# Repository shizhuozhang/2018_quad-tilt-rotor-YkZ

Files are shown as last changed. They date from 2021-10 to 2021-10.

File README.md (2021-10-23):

# <center>小型四倾转旋翼模型机

# (a small scale quad-tilt-rotor prototype)<center>  

&emsp;&emsp; 该项目资助来源于哈工程 (HEU) 自动化学院 2017年的大学生创新创业训练计划的项目，项目经费1万元左右，后该项目延续为我的本科毕业设计。启发来源于美国”鱼鹰V-22“倾转旋翼机和中国在研的“蓝鲸”四倾转旋翼机。由于经费有限，时间有限，资料有限，当时的个人能力有限，仅完成模型机的初步实现，包括：机械模型的设计制作（感谢EV刘同学的帮助），整体电控系统的设计，一个简单的地面站上位机（感谢EV燕同学的帮助），基于Free-RTOS的飞控开发，Hovering控制器设计、仿真和实现，倾转过渡模式的控制策略的仿真，进行了hovering模式下的飞行试验。后来由于飞行试验过程中的事故，导致模型部分损毁，由于没有时间和经费修复，研究就此终止，成为遗憾。

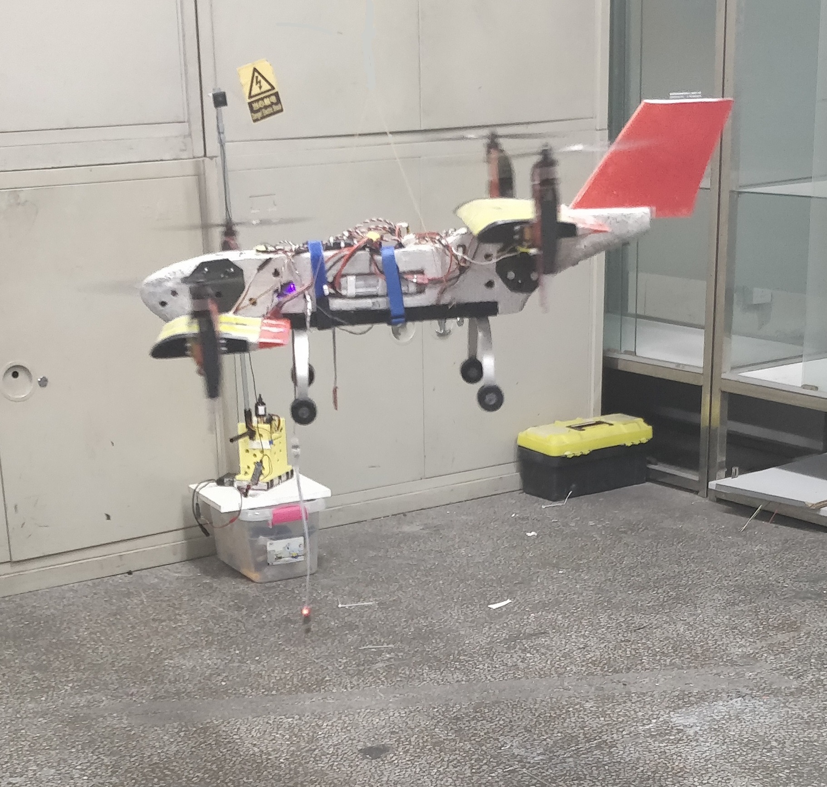
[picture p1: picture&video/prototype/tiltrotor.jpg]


***

&emsp;&emsp;这是我本科所有科创项目中最综合的一个，由于大家当时都很忙，除了必要的帮忙，我几乎一个人承担机械、电控、仿真、软件和试验测试，所以部分工作实在显得简陋。努力总结出几点特色：

* 该项目里对部分元件，如电机，舵机等建模过程有详细描述，可以参考。

* 飞行控制还是常规双环PID，不过不是none-model的调参，对系统做了简单的建模，基于简化线性传函，在simulink中做了仿真，给实际的控制器参数提供参考。

* 模型机结构做的很差，倾转机构没找到特别好的方案，也没人帮忙，只能用大扭矩舵机，导致整机重量偏重，不过这种构型应该是可以进一步测试的。

* 整个电控系统是自己开发的，包括元件选型，PCB的设计焊接等，系统分成控制器板和电源板两部分，控制板（MCU是STM32F407VE）专门处理飞控程序，留有各种传感器接口，电源板集成了电流采样、强电隔离、控制电稳压等电路。无刷电机，电调，AHRS均使用淘宝模块，外加了蓝牙模块用来调试是存数据。

* 关于倾转策略，当时想了一个“非负攻角加速”的策略，先在直升机状态下倾转转子同时调整俯仰角到某一临界角度，然后再加速，使气动力逐渐发挥作用。但是没看到相关文献，自认为是奇思妙想，虽然没能通过实飞测试，但做了半实物仿真。至于现在有没有人做了相关工作，也没有再过多关注。

  总体来说，整个项目也算尽力去做了，但最大的不足还是在机械结构的设计和制作上，这也是倾转旋翼机的最大的难点之一，现阶段感觉可能尾座式无人机（tail-sitter）可能更有希望推广应用。

  ***

  该项目文件夹说明：

  * /code 里是项目设计的全部代码，包括整机飞控，组件的建模调试等，C语言编写，开发环境是针对stm32单片机的IDE软件keil5。（当时水平较菜，代码可能有些凌乱）
  * /document 里是项目的论文，包括毕设论文和答辩PPT，还有一篇为大创项目结题为拼凑的一篇小论文（并没有投任何刊物）。
  * /experiment data 里是实物建模和飞行测试的数据及其分析。
  * /PCB 里是两块电路板的原理图.
  * /picture&video 里是模型机相关的图片和测试视频。
  * /simulation 里是论文中对应的控制理论仿真设计内容，主要是各控制通道的simulink框图仿真和曲线绘图。
  
  ***
  
  感兴趣的同学想要进一步了解项目详情，请联系我：yaokunz@hust.edu.cn

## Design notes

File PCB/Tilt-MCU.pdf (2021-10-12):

## Tilt-MCU Project

# 1. Description

## 1.1. Project

Project Name | Tilt-MCU
Generated with: | MicroXplorer V2.2
Date | 10/24/2017

## 1.2. MCU

MCU family | STM32
MCU name | STM32F407V(E-G)Tx
MCU Package | LQFP100
MCU Pin number | 100

# 2. Pinout Configuration

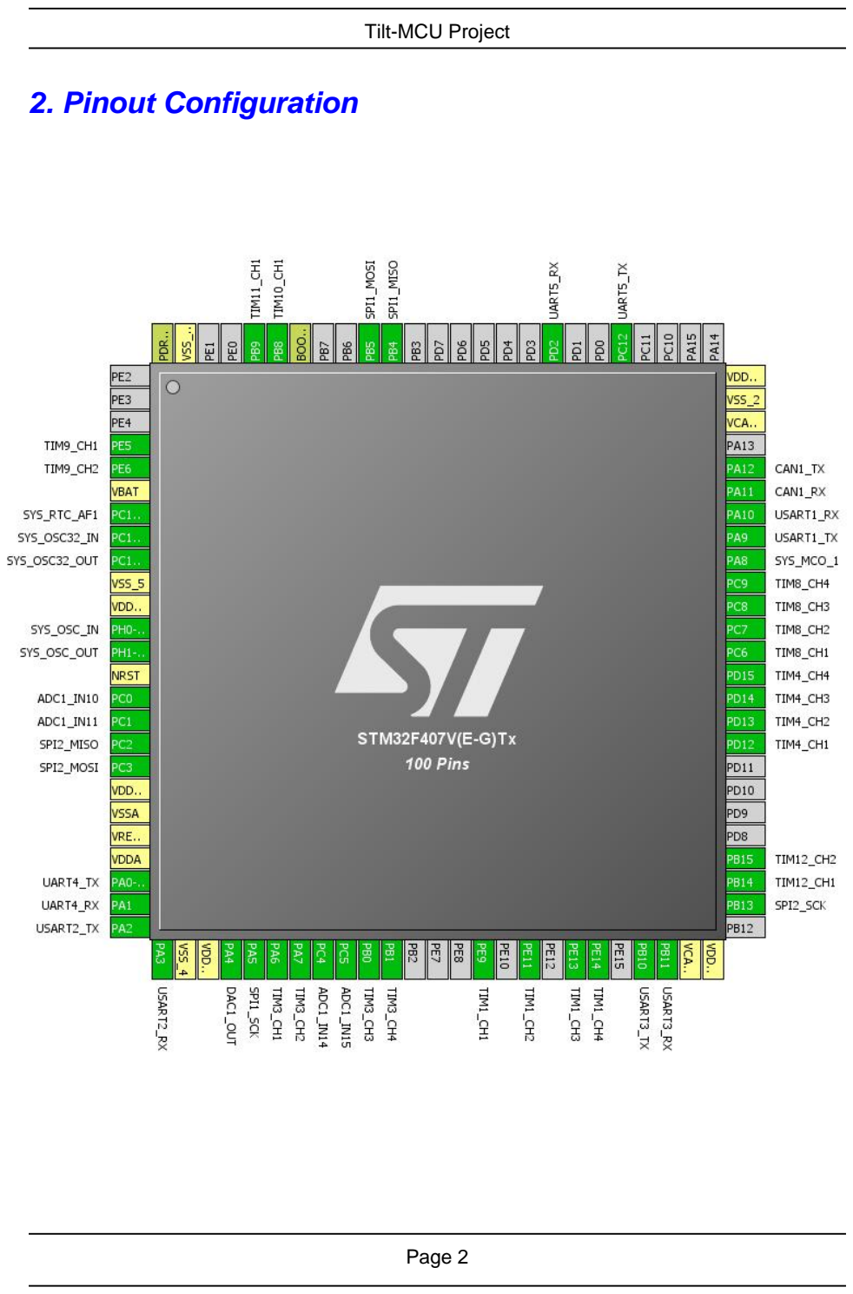
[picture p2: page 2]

# 3. Peripherals Configuration

Peripheral | Mode | Remap | Fonction | Pin
SPI1 | Full-Duplex-Master
1 | SPI1_MISO | PB4
1 | SPI1_MOSI | PB5
0 | SPI1_SCK | PA5
SPI2 | Full-Duplex-Master
0 | SPI2_MISO | PC2
0 | SPI2_MOSI | PC3
1 | SPI2_SCK | PB13
USART1 | Multiprocessor-communication | 0
USART1_RX | PA10
USART1_TX | PA9
USART2 | Multiprocessor-communication | 0
USART2_RX | PA3
USART2_TX | PA2
USART3 | Multiprocessor-communication | 0
USART3_RX | PB11
USART3_TX | PB10
UART4 | Multiprocessor-communication | 0
UART4_RX | PA1
UART4_TX | PA0-WKUP
UART5 | Multiprocessor-communication | 0
UART5_RX | PD2
UART5_TX | PC12
CAN1 | CAN | 0
CAN1_RX | PA11
CAN1_TX | PA12

ADC1

IN10 | 0 | ADC1_IN10 | PC0
IN11 | 0 | ADC1_IN11 | PC1
IN14 | 0 | ADC1_IN14 | PC4
IN15 | 0 | ADC1_IN15 | PC5
TIM1 | PWM-Generation | 0
TIM1_CH1 | PE9
TIM1_CH2 | PE11
TIM1_CH3 | PE13
TIM1_CH4 | PE14
TIM8 | PWM-Generation | 0
TIM8_CH1 | PC6
TIM8_CH2 | PC7
TIM8_CH3 | PC8
TIM8_CH4 | PC9
TIM3 | PWM-Generation | 0
TIM3_CH1 | PA6
TIM3_CH2 | PA7
TIM3_CH3 | PB0
TIM3_CH4 | PB1
TIM4 | PWM-Generation | 0
TIM4_CH1 | PD12
TIM4_CH2 | PD13
TIM4_CH3 | PD14
TIM4_CH4 | PD15
TIM9 | PWM-Input | 0
TIM9_CH1 | PE5

Peripheral | Mode | Remap | Fonction | Pin
| | | TIM9_CH2 | PE6
TIM12 | PWM-Input | 0 | TIM12_CH1 | PB14
| | | TIM12_CH2 | PB15
TIM10 | PWM-Generation | 0 | TIM10_CH1 | PB8
TIM11 | PWM-Generation | 0 | TIM11_CH1 | PB9
DAC1 | Dac | 0 | DAC1_OUT | PA4
SYS | SYS-OSC | 0 | SYS_OSC_IN | PH0-OSC_IN
| | | SYS_OSC_OUT | PH1-OSC_OUT
| SYS-OSC32 | 0 | SYS_OSC32_IN | PC14-OSC32_IN
| | | SYS_OSC32_OUT | PC15-OSC32_OUT
| TAMPER1/TIMERSTAMP/ALARM_OUT/512Hz | 0 | SYS_RTC_AF1 | PC13-ANTI_TAMP
| Clock-out-1 | 0 | SYS_MCO_1 | PA8

# 4. Pins configuration

Pins | Pos | Functions
PE5 | 4 | TIM9_CH1
PE6 | 5 | TIM9_CH2
PC13-ANTI_TAMP | 7 | SYS_RTC_AF1
PC14-OSC32_IN | 8 | SYS_OSC32_IN
PC15-OSC32_OUT | 9 | SYS_OSC32_OUT
PH0-OSC_IN | 12 | SYS_OSC_IN
PH1-OSC_OUT | 13 | SYS_OSC_OUT
PC0 | 15 | ADC1_IN10
PC1 | 16 | ADC1_IN11
PC2 | 17 | SPI2_MISO
PC3 | 18 | SPI2_MOSI
PA0-WKUP | 23 | UART4_TX
PA1 | 24 | UART4_RX
PA2 | 25 | USART2_TX
PA3 | 26 | USART2_RX
PA4 | 29 | DAC1_OUT
PA5 | 30 | SPI1_SCK
PA6 | 31 | TIM3_CH1
PA7 | 32 | TIM3_CH2
PC4 | 33 | ADC1_IN14
PC5 | 34 | ADC1_IN15
PB0 | 35 | TIM3_CH3
PB1 | 36 | TIM3_CH4
PE9 | 40 | TIM1_CH1
PE11 | 42 | TIM1_CH2
PE13 | 44 | TIM1_CH3
PE14 | 45 | TIM1_CH4
PB10 | 47 | USART3_TX
PB11 | 48 | USART3_RX
PB13 | 52 | SPI2_SCK
PB14 | 53 | TIM12_CH1
PB15 | 54 | TIM12_CH2
PD12 | 59 | TIM4_CH1
PD13 | 60 | TIM4_CH2
PD14 | 61 | TIM4_CH3
PD15 | 62 | TIM4_CH4
PC6 | 63 | TIM8_CH1
PC7 | 64 | TIM8_CH2
PC8 | 65 | TIM8_CH3

Pins | Pos | Functions
PC9 | 66 | TIM8_CH4
PA8 | 67 | SYS_MCO_1
PA9 | 68 | USART1_TX
PA10 | 69 | USART1_RX
PA11 | 70 | CAN1_RX
PA12 | 71 | CAN1_TX
PC12 | 80 | UART5_TX
PD2 | 83 | UART5_RX
PB4 | 90 | SPI1_MISO
PB5 | 91 | SPI1_MOSI
PB8 | 95 | TIM10_CH1
PB9 | 96 | TIM11_CH1

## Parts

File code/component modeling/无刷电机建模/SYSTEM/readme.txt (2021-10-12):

在新建工程的时候，请在：Options for Target-->C/C++ 选项卡里面 Preprocessor Symbols 栏定义你的STM32芯片容量。比如:ALIENTEK 战舰STM32开发板用户，使用的是大容量的STM32芯片，则在Define栏输入：STM32F10X_HD 

对于STM32F103系列芯片，设置原则如下：
16KB≤FLASH≤32KB       选择：STM32F10X_LD
64KB≤FLASH≤128KB      选择：STM32F10X_MD
256KB≤FLASH≤512KB     选择：STM32F10X_HD

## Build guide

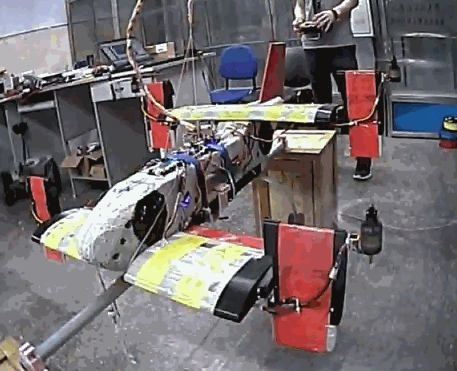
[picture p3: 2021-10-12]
picture&video/experiment/ROLL-STEP1.gif

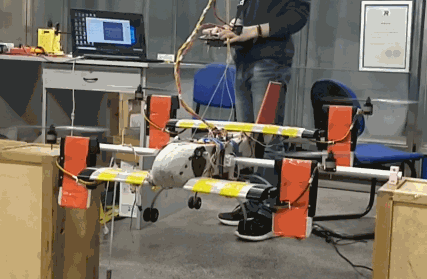
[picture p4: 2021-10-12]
picture&video/experiment/PITCH-STEP2.gif

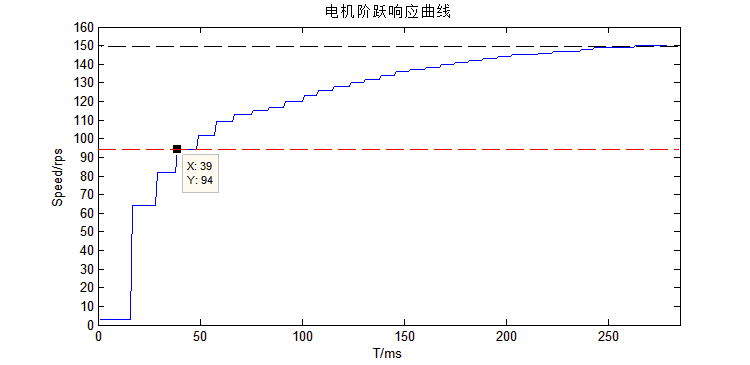
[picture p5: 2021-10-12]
experiment data/电机建模/motor's_step_response.bmp

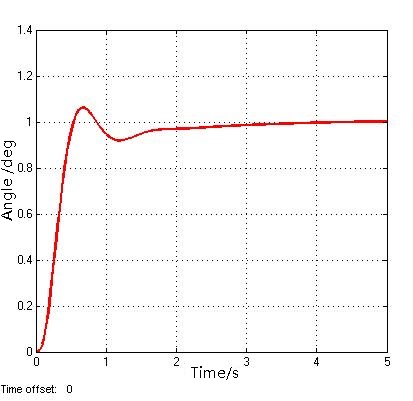
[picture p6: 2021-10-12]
simulation/airpitch_step.JPG

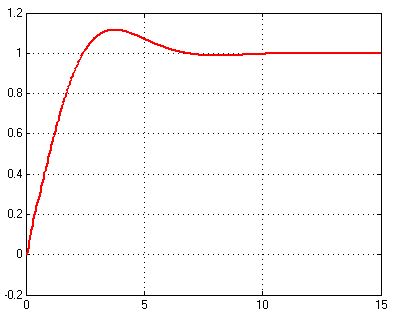
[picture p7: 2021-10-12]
simulation/height-step.JPG

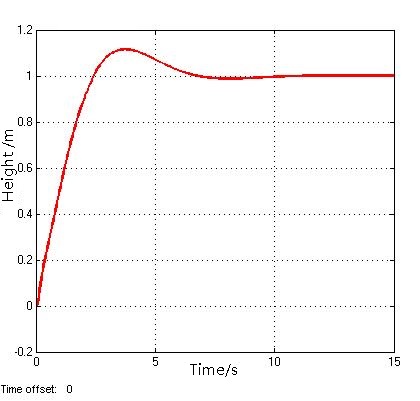
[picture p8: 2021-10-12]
simulation/height-sigpid-step.jpg

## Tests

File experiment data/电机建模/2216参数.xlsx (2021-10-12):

X2216 | KV880 | KV1100 | KV1250 | KV1400 | KV1800 | KV2400
定子外径 | 22mm | 22mm | 22mm | 22mm | 22mm | 22mm
定子厚度 | 16mm | 16mm | 16mm | 16mm | 16mm | 16mm
定子槽数 | 12 | 12 | 12 | 12 | 12 | 12
定子级数 | 14 | 14 | 14 | 14 | 14 | 10
电机 | 880 | 1100 | 1250 | 1400 | 1800 | 2400
空载电流 | 0.5A | 0.9A | 1.1A | 1.3A | 1.6A | 1.7A
电机电阻 | 117mΩ | 73mΩ | 63mΩ | 55mΩ | 29mΩ | 29mΩ
最大连续电流 | 20A/30S | 24A/30S | 28A/30S | 33A/30S | 35A/30S | 40A/30S
最大连续功率 | 320W | 385W | 392W | 540W | 350W | 710W
重量（含长线） | 72g | 72g | 72g | 72g | 70g | 67g
转子直径 | 27.7mm | 27.7mm | 27.7mm | 27.7mm | 27.7mm | 27.7mm
出轴直径 | 3.175mm | 3.175mm | 3.175mm | 3.175mm | 3.175mm | 3.175mm
电机长度 | 34mm | 34mm | 34mm | 34mm | 34mm | 34mm
电机含轴总长度 | 36.5mm | 36.5mm | 36.5mm | 36.5mm | 36.5mm | 36.5mm
最大电池节数 | 2S-4S | 2S-4S | 2S-4S | 2S-4S | 2S-4S | 3S-4S
建议使用电调 | 30A | 30A | 40A | 40A | 40A | 60A
推荐螺旋桨规格 | APC10X4.7、APC1070、APC1147、APC11x5.5 | APC9047、APC9045、APC9060、APC8060、APC1047 | APC9047、APC9045、APC9060、APC8060、APC1047 | APC9047、APC9045、APC9060、APC8060、APC7060 | APC7050、APC7060、APC6040 | APC6040
适用特技机重量 | 720g(4S 9060\1047\1050) | 800g 3s 1047\1050 | 720g(3s 9060\9047\9045)(4s 8060) | 760g(3s 9060\9047\9045)(4s 8060) | 680g(3s APC 7060\7050)(4S APC 6040) | ——
适用多旋翼重量 | 单轴重量450g(4s 8038\8043\8045\9047) | —— | —— | —— | —— | 适合微推特技机 650g (4s apc6040)
适用于3D机重量 | 600g(3s 1147) | 650g(3s 1047\1050) | 650g(3s 9047\1047) | 650g(3s 9047) | —— | ——

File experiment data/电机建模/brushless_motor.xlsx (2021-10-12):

遥控器数据 | 油门大小 | 等效电压/V | 转速/RPS | 升力/g |  | 等效电压/V
-660 | 0.00 | 0.00 | 2 | 0 | 0 | 0.00 | 0 | 0
-353 | 0.23 | 2.84 | 21 | 46 | 0.4508 | 2.84 | 0.24 | 0.4508
-297 | 0.28 | 3.35 | 27 | 85 | 0.833 | 3.35 | 0.75 | 0.833
-219 | 0.33 | 4.08 | 35 | 134 | 1.3132 | 4.08 | 1.48 | 1.3132
-148 | 0.39 | 4.73 | 43 | 200 | 1.96 | 4.73 | 2.13 | 1.96
-117 | 0.41 | 5.02 | 45 | 235 | 2.303 | 5.02 | 2.42 | 2.303
-70 | 0.45 | 5.45 | 52 | 300 | 2.94 | 5.45 | 2.85 | 2.94
-35 | 0.47 | 5.78 | 55 | 350 | 3.43 | 5.78 | 3.18 | 3.43
0 | 0.50 | 6.10 | 58 | 400 | 3.92 | 6.10 | 3.50 | 3.92
41 | 0.53 | 6.48 | 62 | 450 | 4.41 | 6.48 | 3.88 | 4.41
75 | 0.56 | 6.79 | 65 | 500 | 4.9 | 6.79 | 4.19 | 4.9
120 | 0.59 | 7.21 | 69 | 560 | 5.488 | 7.21 | 4.61 | 5.488
150 | 0.61 | 7.49 | 71 | 600 | 5.88 | 7.49 | 4.89 | 5.88
200 | 0.65 | 7.95 | 74 | 670 | 6.566 | 7.95 | 5.35 | 6.566
252 | 0.69 | 8.43 | 78 | 750 | 7.35 | 8.43 | 5.83 | 7.35
290 | 0.72 | 8.78 | 81 | 800 | 7.84 | 8.78 | 6.18 | 7.84
349 | 0.76 | 9.33 | 85 | 900 | 8.82 | 9.33 | 6.73 | 8.82
398 | 0.80 | 9.78 | 88 | 950 | 9.31 | 9.78 | 7.18 | 9.31
450 | 0.84 | 10.26 | 92 | 1000 | 9.8 | 10.26 | 7.66 | 9.8
489 | 0.87 | 10.62 | 92 | 1050 | 10.29 | 10.62 | 8.02 | 10.29
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

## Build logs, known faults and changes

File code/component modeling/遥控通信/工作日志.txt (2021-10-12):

2017.12.09.12
加入遥控器数据接收，飞机可动，验证飞行重量的可行性。

2017.12.09.17
加入AHRS数据接受，加入电压，电流计算和电源监测

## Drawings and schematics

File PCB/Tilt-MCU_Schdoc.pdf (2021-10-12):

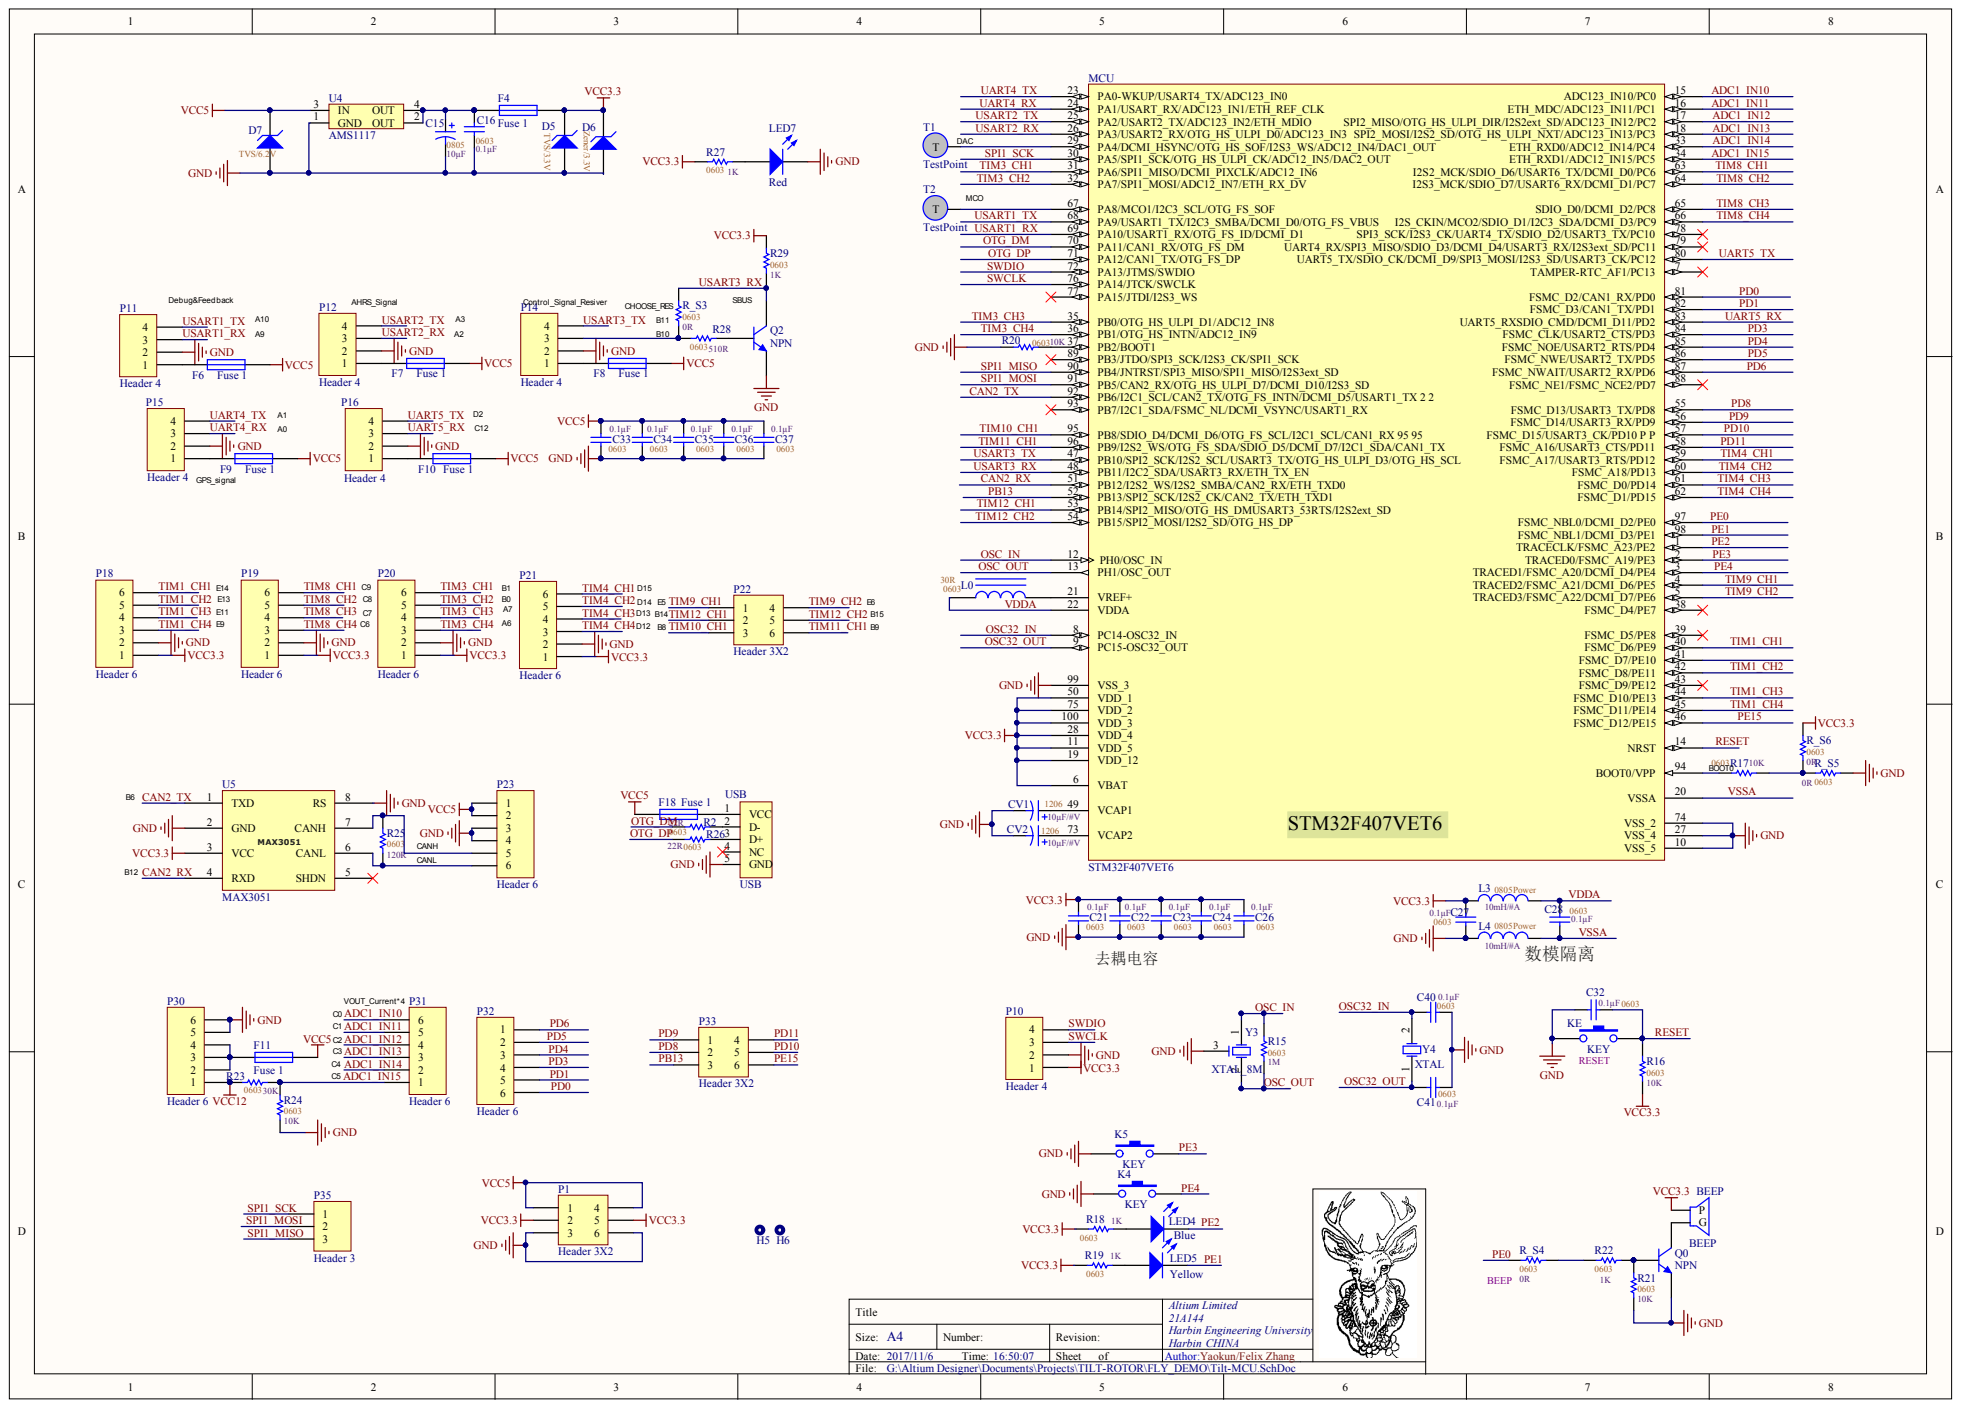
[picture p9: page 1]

VDD_2 75
VDD_3 100
VDD_4 28
VDD_5 11
VDD_12 19

Size: A4 | Number: | Revision:
Date: 2017/11/6 Time: 16:50:07 | Sheet of | Author:Yaokun/Felix Zhang
File: G:\Altium Designer\Documents\Projects\TILT-ROTOR\FLY_DEMO\Tilt-MCU.SchDoc

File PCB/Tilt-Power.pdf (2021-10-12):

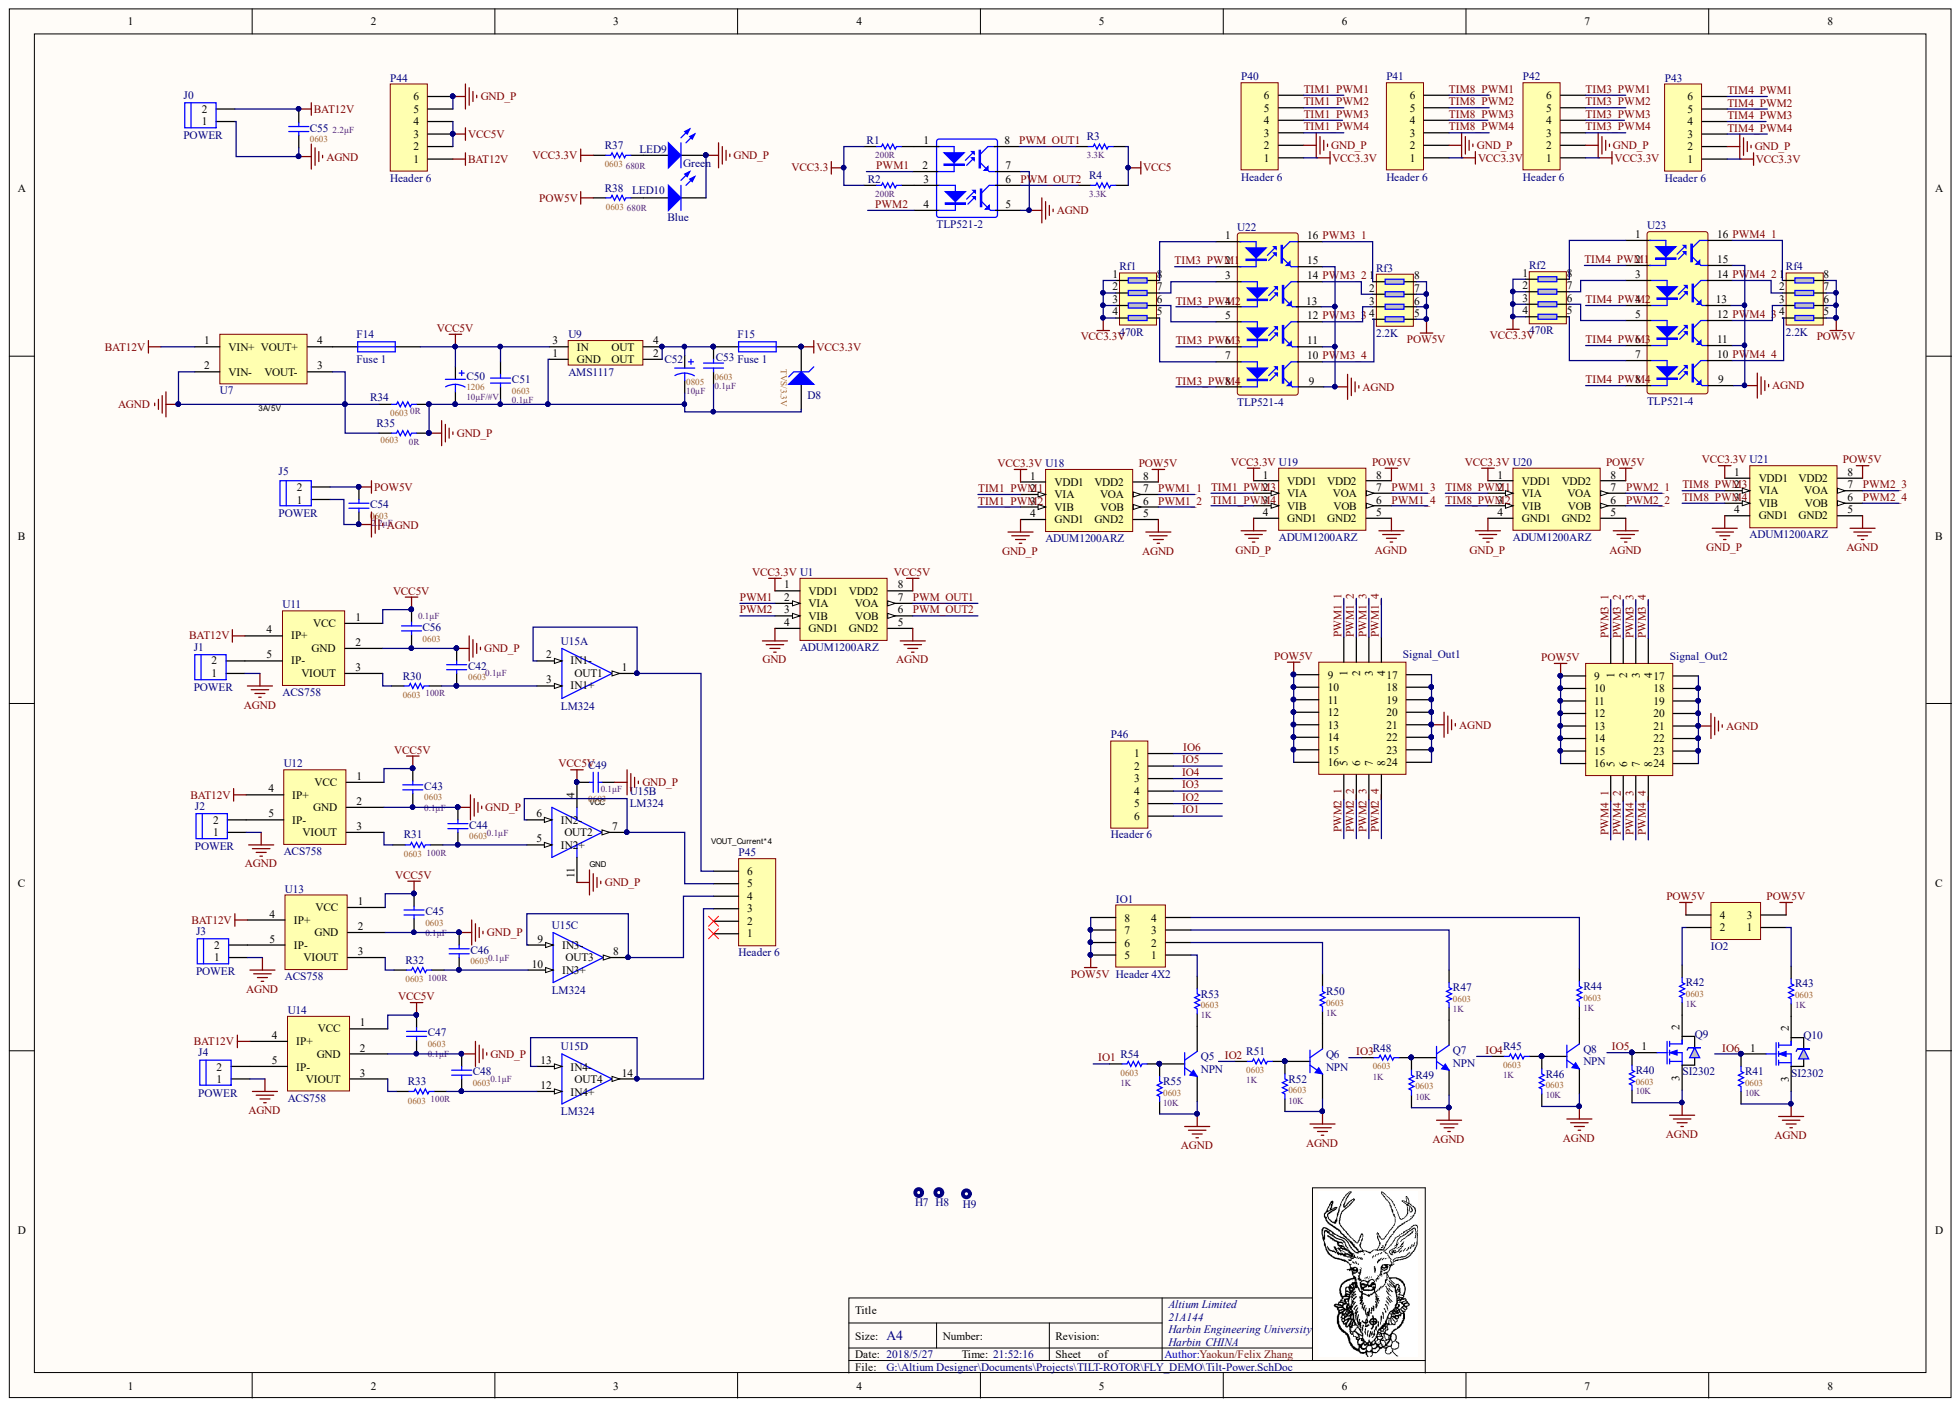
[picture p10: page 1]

Title | Altium Limited 21A144 Harbin Engineering University Harbin CHINA

Size: A4 | Number: | Revision:
Date: 2018/5/27 Time: 21:52:16 | Sheet of | Author:Yaokun/Felix Zhang
File: G:\Altium Designer\Documents\Projects\TILT-ROTOR\FLY_DEMO\Tilt-Power.SchDoc

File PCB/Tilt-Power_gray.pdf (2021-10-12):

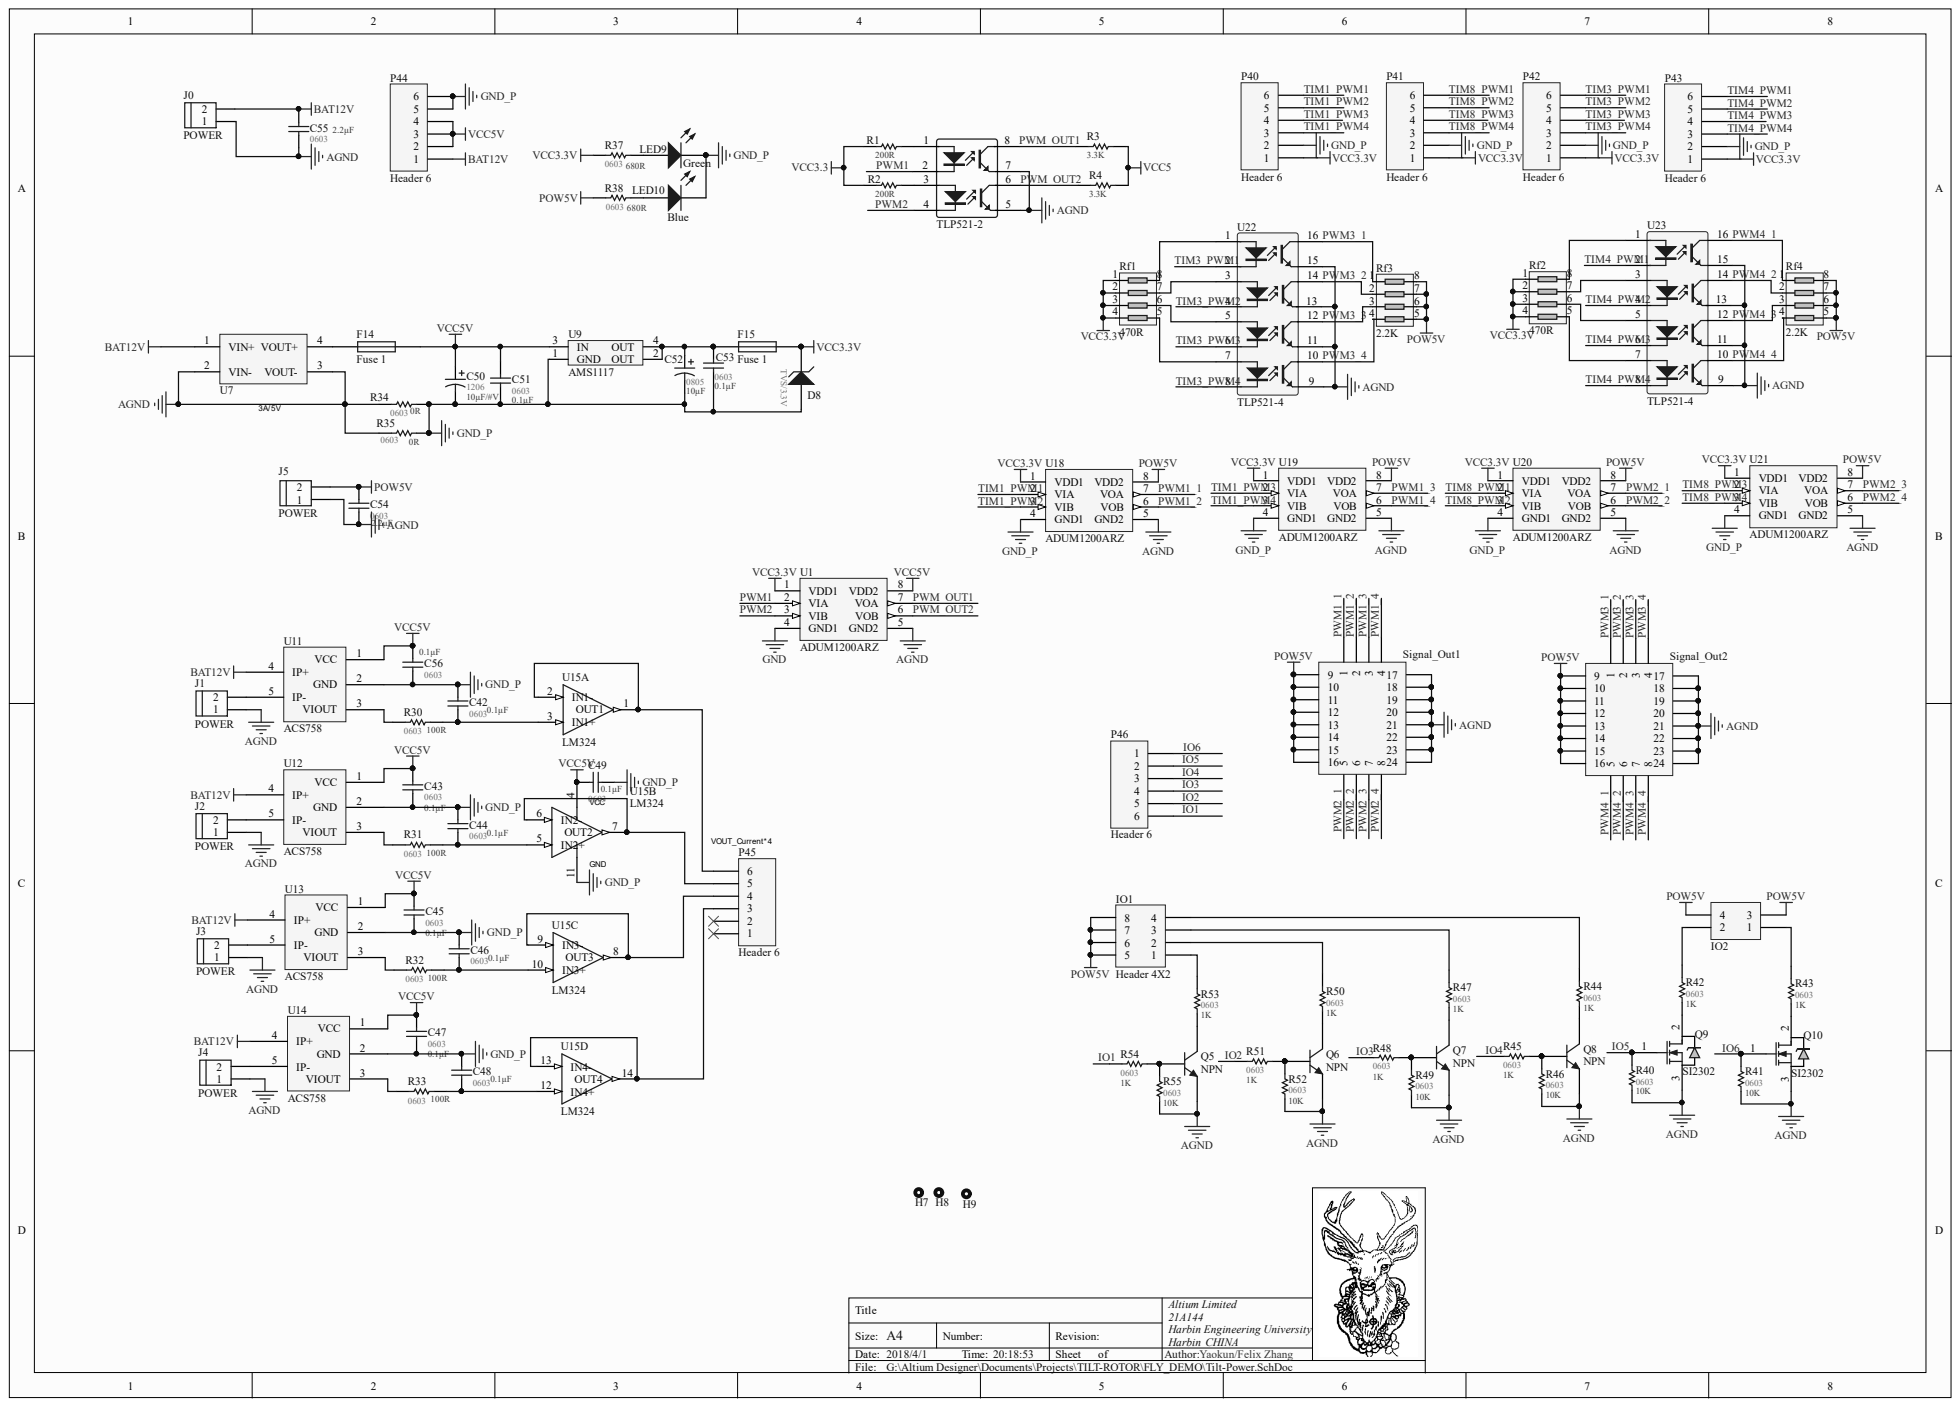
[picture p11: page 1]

Title | Altium Limited 21A144 Harbin Engineering University Harbin CHINA

Size: A4 | Number: | Revision:
Date: 2018/4/1 Time: 20:18:53 | Sheet of | Author:Yaokun/Felix Zhang
File: G:\Altium Designer\Documents\Projects\TILT-ROTOR\FLY_DEMO\Tilt-Power.SchDoc

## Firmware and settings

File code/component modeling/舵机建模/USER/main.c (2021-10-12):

#include "H_define.h"


#define Init_S1 3000
extern u16 time_num;
float Angle_Init[3]={0.0,0.0,0.0};
float Angle_Sum[3]={0.0};
	u8 GYRO_Flag=1;
int main()
{

	u8 Num=0;//陀螺仪初始化
	
	Init1();
	
	TIM4->CCR1=Init_S1;  
	delay_ms(1000);
	
    while(1)
	{					
		if(sign_usrt2)
		{	
			if(Num>100)
			{
				GYRO_Flag=0;
				Num=100;
				Angle_Init[0]=(float)(Angle_Sum[0]/100);
				Angle_Init[1]=(float)(Angle_Sum[1]/100);	
				Angle_Init[2]=(float)(Angle_Sum[2]/100);
				printf("%f  %f  %f \r\n",Angle_Init[0],Angle_Init[1],Angle_Init[2]);	
				printf("ok\r\n");	
				TIM3->CR1|=1<<0;//使能计数器				
			}
			
			if(GYRO_Flag)
			{
				Num++;	
				Angle_Sum[0]+=Angle_Now.Angle_X;
				Angle_Sum[1]+=Angle_Now.Angle_Y;
				Angle_Sum[2]+=Angle_Now.Angle_Z;
			}	
					
			
			sign_usrt2=0;	
			
		
		}
	}
}

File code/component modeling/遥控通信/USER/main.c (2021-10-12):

#include "H_define.h"

int main(void)
{ 
	u8 t=0;
	Init1();
	Init2();
	while(1)
	{
		
		delay_ms(200);
		
		printf("tim8 %d %d %d %d\r\n",TIM8->CCR1,TIM8->CCR2,TIM8->CCR3,TIM8->CCR4);
		
		printf("tim3 %d %d %d %d\r\n",TIM3->CCR1,TIM3->CCR2,TIM3->CCR3,TIM3->CCR4);
		
//		if(sign_Adc1)
//		{
//			sign_Adc1=0;
//			Power_Monitor();
////			for(t=0;t<6;t++)
////			{
////				printf("%d %f %f %f\r\n",t,Voltage[t],Current[t],Walte[t]);
////			}
			printf("\r\n");
//		}	
//		if(sign_usrt2==1)
//		{
//			for(t=0;t<42;t++)
//			{
//				printf("%d   ",t);
//				printf("%x\r\n", AHRS_DATA[t]);
//			}
//			printf("OK\r\n");
//			
//			sign_usrt2=0;		
//		}
		
		
//		printf("t:%d\r\n",t);
////		LED0=~LED0;
////		LED1=~LED1;
//		delay_ms(200);
//		t++;
	}
}

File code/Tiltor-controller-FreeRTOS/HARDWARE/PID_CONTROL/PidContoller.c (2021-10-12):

#include "stm32f4xx_conf.h"

/****************************
参数整定找最佳，从小到大顺序查
先是比例后积分，最后再把微分加
曲线振荡很频繁，比例度盘要放大
曲线漂浮绕大湾，比例度盘往小扳
曲线偏离回复慢，积分时间往下降
曲线波动周期长，积分时间再加长
曲线振荡频率快，先把微分降下来
动差大来波动慢。微分时间应加长
理想曲线两个波，前高后低4比1
一看二调多分析，调节质量不会低
****************************/
//增量式PID算法
void Increment_PID(PID_IncrementType* PID)
{
	 /*增量式PID计算*/
	 PID->d_CtrOut = PID->Kp * PID->ErrNow - PID->Ki * PID->ErrLast + PID->Kd * PID->ErrPrev;
	
	 PID->ErrPrev = PID->ErrLast; //存储误差，用于下次计算
	 PID->ErrLast = PID->ErrNow;  //

//	 PID->ctrOut += PID->dCtrOut;
}


//绝对式PID算法
void Absolute_PID(PID_AbsoluteType* PID)
{

	 PID->ErrP = PID->ErrNow;  //读取现在的误差，用于kp控制

	 PID->ErrI += PID->ErrNow; //用矩形法数值积分近似代替积分，用累加的方法记忆长期误差，用于ki控制

	  if( PID->ErrI > PID->ErrIMax)    //对积分限幅，避免出现积分饱和
		  PID->ErrI = PID->ErrIMax;		//Max和Min的设置应与积分增益匹配，满足单独积分输出时使驱动器达到最低和最高
	  else if(PID->ErrI < PID->ErrIMin)    
		  PID->ErrI = PID->ErrIMin;
	 
	 PID->ErrD = PID->ErrNow - PID->ErrLast;//一阶后向差分近似代替微分，用于kd控制
									//要保证采样时间间隔基本恒定，设置最高优先级，否则会引入噪声
	 PID->ErrLast = PID->ErrNow;	//保存现在的误差
	 
	 PID->CtrOut = PID->Kp * PID->ErrP + PID->Ki * PID->ErrI + PID->Kd * PID->ErrD;//计算绝对式PID输出

}

//#define Low_Pass 0.85

////extern volatile Angle_XYZ  Angle_Exp;///位置环输出的期望角度

//PID_AbsoluteType  PID_Pitch,PID_Roll;	//外环：角度PID环
////Pitch绕Y轴下层外环一号电机， roll绕X轴，内环二号电机
//PID_AbsoluteType  PID_Pitch_Rate,PID_Roll_Rate;		//PID内环：角速度PID环

//WAng_XYZ  WAng_Proce;
//WAng_XYZ  WAng_Proce_Last;

//void PID_Double_Angle(WAng_XYZ  Now_WAng,  Angle_XYZ Now_angle, Angle_XYZ Exp_angle)
//{
//	float Angle_Cycle_out[3]={0};//三个轴向XYZ的角度外环输出值
/*	
	PID_Pitch.ErrNow=Now_angle.Angle_Y -Exp_angle.Angle_Y ;///由于电机转向已确定，故在这里换向
	PID_Roll.ErrNow= Exp_angle.Angle_X - Now_angle.Angle_X;
	
	PID_Pitch.Kp=50;//60
	PID_Pitch.Ki=0.3;
	PID_Pitch.Kd=0;
	PID_Pitch.ErrIMax=1200;
	PID_Pitch.ErrIMin=-1200;
	
	PID_Roll.Kp=37;
	PID_Roll.Ki=0.225;
	PID_Roll.Kd=0;
	PID_Roll.ErrIMax=1200;
	PID_Roll.ErrIMin=-1200;
	
	Absolute_PID(&PID_Pitch);//执行绝对式PID算法
	Absolute_PID(&PID_Roll);//执行绝对式PID算法
//	Motor_Value[0]=(s16)PID_Pitch.CtrOut;
//	Motor_Value[1]=(s16)PID_Roll.CtrOut;	
	
///*********阻尼项做一个低通给D使用	
	WAng_Proce_Last.WAngle_X = WAng_Proce.WAngle_X;//	//更新数之前先存储
	WAng_Proce.WAngle_X= Low_Pass * WAng_Proce_Last.WAngle_X +(1- Low_Pass)* Now_WAng.WAngle_X;
//	//低通滤波

	WAng_Proce_Last.WAngle_Y = WAng_Proce.WAngle_Y;//	//更新数之前先存储	
	WAng_Proce.WAngle_Y= Low_Pass * WAng_Proce_Last.WAngle_Y +(1- Low_Pass)* Now_WAng.WAngle_Y;
//	//低通滤波

///内环
	PID_Pitch_Rate.ErrNow=PID_Pitch.CtrOut+WAng_Proce.WAngle_Y*0.0610351;
	PID_Roll_Rate.ErrNow=PID_Roll.CtrOut+WAng_Proce.WAngle_X*0.0610351;
	
	PID_Pitch_Rate.Kp=1.3;//1.0
	PID_Pitch_Rate.Ki=0;
	PID_Pitch_Rate.Kd=0;
	PID_Pitch_Rate.ErrIMax=100;
	PID_Pitch_Rate.ErrIMin=-100;
	
	PID_Roll_Rate.Kp=1.2;//1.0
	PID_Roll_Rate.Ki=0;
	PID_Roll_Rate.Kd=0;
	PID_Roll_Rate.ErrIMax=100;
	PID_Roll_Rate.ErrIMin=-100;
	
	Absolute_PID(&PID_Pitch_Rate);//执行绝对式PID算法
	Absolute_PID(&PID_Roll_Rate);//执行绝对式PID算法
	
	Motor_Value[0]=(s16)PID_Pitch_Rate.CtrOut;
	Motor_Value[1]=(s16)PID_Roll_Rate.CtrOut;	
*/
//}

void Motor_Drive(s16 To_Motor[3])
{
//	u8 i=0;
//	for(i=0;i<3;i++)//输出限幅和死区限位
//	{
//		if(To_Motor[i]>0)
//		{
//			if(To_Motor[i]>3580)
//				To_Motor[i]=3580;
//			else if(To_Motor[i]<120)	
//				To_Motor[i]+=120;
//		}
//		
//		if(To_Motor[i]<0)
//		{
//			if(To_Motor[i]<-3580)
//				To_Motor[i]=-3580;
//			else if(To_Motor[i]>-120)	
//					To_Motor[i]-=120;
//		}
//	
//	}
//	
//	if(To_Motor[0]>0)//电机1
//	{
//			TIM8->CCR1=0;
//			TIM8->CCR2=To_Motor[0];
//	}
//	else
//	{		
//			TIM8->CCR1=-To_Motor[0];
//			TIM8->CCR2=0;
//	}
//	
//	if(To_Motor[1]>0)//电机2
//	{
//			TIM8->CCR3=0;
//			TIM8->CCR4=To_Motor[1];
//	}
//	else
//	{
//			TIM8->CCR3=-To_Motor[1];
//			TIM8->CCR4=0;
//	}		
}


	
///*****************************************************************************/	
//	
///*****************************输出给电机************************************************/
//		 
//		motor_yaw = (s16) PID_Yaw_Rate.Out;
//    if(!motor_en)
//			motor_yaw=0;
//	  Motor_PWM_Update(motor_yaw);
//		motor_pitch = -(s16)(PID_Pitch_Rate.Out);
//	  set_current(motor_pitch *5);
//}


///*
// * 函数名：PID_Init
// * 描述  ：PID参数初始化函数
// * 输入  ：无
// * 输出  ：无
// */ 
//void PID_Init(void)
//{
//	
//	PID_Yaw_Angle.P =55;		//65
//	PID_Yaw_Angle.I = 0.00;//0.05
//		
//角速度环	
//	
//	PID_Yaw_Rate.P = 1.1;//1.2
//	PID_Yaw_Rate.I = 0;

//	
//	PID_Yaw_Angle.Pout = 0;
//	PID_Yaw_Angle.Iout = 0;
//	PID_Yaw_Angle.Dout = 0;
//		
//	
//	PID_Yaw_Rate.Pout = 0;
//	PID_Yaw_Rate.Iout = 0;
//	PID_Yaw_Rate.Dout = 0;

//	//角度环参数
//	PID_Pitch_Angle.P =27;
//	PID_Pitch_Angle.I =0.05;//0.1的时候超调有0.01度
//	PID_Pitch_Angle.D =0;
//	
//角速度环	
//	PID_Pitch_Rate.P =-8;
//	PID_Pitch_Rate.I =0;
//	PID_Pitch_Rate.D =0;
// 
//	PID_Pitch_Angle.Pout = 0;
//	PID_Pitch_Angle.Iout = 0;
//	PID_Pitch_Angle.Dout = 0;
//	
//	PID_Pitch_Rate.Pout = 0;
//	PID_Pitch_Rate.Iout = 0;
//	PID_Pitch_Rate.Dout = 0;
//}
					




/***********************************************************************************

*****************************************电机速度环伺服***********************************

PID_AbsoluteType SPEED_PID;//定义PID算法的结构体

s16 SpeedControl(s16 SpeedTag,s16 SpeedNow)
{
	SPEED_PID.ErrNow = SpeedTag - SpeedNow;
	
	SPEED_PID.Kp=15; //写入比例系数为
	SPEED_PID.Ki=0.8; //写入积分系数为
	SPEED_PID.Kd=0;//写入微分系数为5
	SPEED_PID.ErrIMax=15000; //写入误差积分上限为1000 
	SPEED_PID.ErrIMin=-15000;	//下限为-1000
	Absolute_PID(&SPEED_PID);//执行绝对式PID算法
	
	return  SPEED_PID.CtrOut;         //读取控制值
}

void OutToMotor1(s16 Control_value)
{
		if(Control_value<0)
		{
			Control_value=-Control_value;
			if(Control_value>=3600)//输出限幅
				Control_value=3600;
			
			TIM4->CCR1=Control_value;	
			TIM4->CCR2=0;			
		}
		else
		{
			if(Control_value>=3600)//输出限幅
				Control_value=3600;
						
			TIM4->CCR1=0;	
			TIM4->CCR2=Control_value;
		}
}

void OutToMotor2(s16 Control_value)
{
		if(Control_value<0)
		{
			Control_value=-Control_value;
			if(Control_value>=3600)//输出限幅
				Control_value=3600;
			TIM4->CCR3=0;	
			TIM4->CCR4=Control_value;	
					
		}
		else
		{
			if(Control_value>=3600)//输出限幅
				Control_value=3600;
		
			TIM4->CCR3=Control_value;	
			TIM4->CCR4=0;				
		}
}
*************/

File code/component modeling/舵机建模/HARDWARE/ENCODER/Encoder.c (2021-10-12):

#include "H_define.h"

#if __ENCODER1

void Encoder1_Init(void)					////TIM8用于编码器模式
{
	RCC->APB2ENR|=1<<11; 	//TIM1时钟使能  
	RCC->APB2ENR|=1<<2;		//IO端口A的时钟使能                                                                  	
    GPIOA->CRH&=0xffffff00;
    GPIOA->CRH|=0x00000044;
	TIM1->ARR=0xffff;		//自动重装载值
	TIM1->CNT=32760;		//初值
	TIM1->SMCR|=3<<0;//编码器模式3
	TIM1->CCMR1|=1<<0;//输入通道映射
	TIM1->CCMR1|=1<<8;//输入通道映射
	TIM1->CR1|=1<<0;//使能计数器
} 
		
#endif  

#if __ENCODER2
void Encoder2_Init(void)					////TIM2用于编码器模式
{
	RCC->APB1ENR|=1<<0;//tim2 enable
	RCC->APB2ENR|=1<<2;//GPIOA enable
	RCC->APB2ENR|=1<<3;//GPIOB enable
	RCC->APB2ENR|=1<<0;		//AFIO端口复用时钟使能
    GPIOA->CRH&=0x0fffffff;
    GPIOA->CRH|=0x40000000;
	GPIOB->CRL&=0xffff0fff;
    GPIOB->CRL|=0x00004000;
	JTAG_Set(SWD_ENABLE);	//关闭jtag
	AFIO->MAPR|=3<<8;		//将TIM2部分重映射
	//注意此时的重映射中带有SWD的引脚PB3(CH2)，按ret下载
	TIM2->ARR=0xffff;
	TIM2->CNT=32760;
	TIM2->SMCR|=3<<0;//编码器模式3
	TIM2->CCMR1|=1<<0;//输入通道映射
	TIM2->CCMR1|=1<<8;//输入通道映射
	TIM2->CR1|=1<<0;//使能计数器
}
#endif

#if __ENCODER3
void Encoder3_Init(void)					////TIM3用于编码器模式
{
	RCC->APB1ENR|=1<<1;//tim3 enable
	RCC->APB2ENR|=1<<2;//GPIOA enable
    GPIOA->CRL&=0x00ffffff;
    GPIOA->CRL|=0x44000000;
	TIM3->ARR=0xffff;
	TIM3->CNT=32760;
	TIM3->SMCR|=3<<0;//编码器模式3
	TIM3->CCMR1|=1<<0;//输入通道映射
	TIM3->CCMR1|=1<<8;//输入通道映射
	TIM3->CR1|=1<<0;//使能计数器
}	
#endif

#if __ENCODER4
void Encoder4_Init(void)					////TIM4用于编码器模式
{
	RCC->APB1ENR|=1<<2;//tim4 enable
	RCC->APB2ENR|=1<<3;//GPIOB enable
    GPIOB->CRL&=0x00ffffff;
    GPIOB->CRL|=0x44000000;
	TIM4->ARR=0xffff;
	TIM4->CNT=32760;
	TIM4->SMCR|=3<<0;//编码器模式3
	TIM4->CCMR1|=1<<0;//输入通道映射
	TIM4->CCMR1|=1<<8;//输入通道映射
	TIM4->CR1|=1<<0;//使能计数器
}	
#endif

#if __ENCODER5
void Encoder5_Init(void)					////TIM5用于编码器模式
{
	RCC->APB1ENR|=1<<3;//tim5 enable
	RCC->APB2ENR|=1<<2;//GPIOA enable
    GPIOA->CRL&=0xffffff00;
    GPIOA->CRL|=0x00000044;
	TIM5->ARR=0xffff;
	TIM5->CNT=32760;
	TIM5->SMCR|=3<<0;//编码器模式3
	TIM5->CCMR1|=1<<0;//输入通道映射
	TIM5->CCMR1|=1<<8;//输入通道映射
	TIM5->CR1|=1<<0;//使能计数器
}	
#endif


#if __ENCODER8

void Encoder8_Init(void)					////TIM8用于编码器模式
{
	RCC->APB2ENR|=1<<13;//tim8 enable
	RCC->APB2ENR|=1<<4;//GPIOC enable
    GPIOC->CRL&=0x00ffffff;
    GPIOC->CRL|=0x44000000;
	TIM8->ARR=0xffff;
	TIM8->CNT=32760;
	TIM8->SMCR|=3<<0;//编码器模式3
	TIM8->CCMR1|=1<<0;//输入通道映射
	TIM8->CCMR1|=1<<8;//输入通道映射
	TIM8->CR1|=1<<0;//使能计数器
}

#endif




//int encoder=0;
//u16 control_num=0;
//u16 encoder_num=0;

////定时器7中断服务函数
//void TIM7_IRQHandler(void)
//{
//	if(TIM_GetITStatus(TIM7,TIM_IT_Update)==SET) //溢出中断
//	{  
//        encoder_num+=1;
//        control_num+=1; 
//        
//        if((encoder_num>=50)&&(display_flag==0))//10Hz的读取频率100ms
//        {
//            encoder_num=0;
//            encoder=(int)(32760-TIM8->CNT);//速度有正负之分，表示正反转         
//            TIM8->CNT=32760;				//重新赋中值
//            
//            LED1=!LED1;
//            display_flag=1;
//        }
//        
//		if(control_num>=5)//控制频率100Hz
//		{ 
//            control_num=0;
//            control_flag=1;	//标志位置1，用于主函数里控制函数运行          
//		}		
//	}
//	TIM_ClearITPendingBit(TIM7,TIM_IT_Update);  //清除中断标志位
//}		

/*
入口参数
Line_num 编码器分辨率，即线数
X_KHz 定时器频率
用在定时器中断中
注意修改编码器所使用的定时器TIMx->CNT
*/
//s16 M_T_Speed_measure(u16 Line_num,u16 X_KHz)//   	M/T测速算法
//{
//	static u8 Tc=100;   //固定时长
//	static u8 t1=0 ;	//第一个脉冲前时长
//    static u8 t2=0;	//最后一个脉冲前时长	   
//	static u8 T=0;	//最终时长,
//	static u16 cntL=0;	//编码器过去值
//	static s16 Z=0;		//最终脉冲个数
//	
//	if(cntL==TIM4->CNT)
//	{
//		if(Tc==100)
//		{
//			t2++;					//最后一个脉冲前时长计数	
//			if(t2>50)				//超时处理
//			{
//				T=Tc-t1+t2-1;
//				Z=cntL-32760;			//编码器重装值是100
//				Tc=0;
//				t1=0;
//				t2=0;
//				TIM4->CNT=32760;		//编码器重装值是100
//				cntL=TIM4->CNT;
//			}
//		}
//		else
//		{
//			t1++;					//第一个脉冲前时长计数	
//		}
//	}
//	else
//	{
//		if(Tc==100)					//一次计时结束
//		{
//			T=Tc-t1+t2;
//			Z=cntL-32760;
//			Tc=0;
//			t1=0;
//			t2=0;
//			TIM4->CNT=32760;
//			cntL=TIM4->CNT;
//		}
//	}
//	if(Tc<100)		//固定时长计数
//	{
//		Tc++;
//		if(Tc==100)
//		{
//			cntL=TIM4->CNT;
//		}
//	}
//	return (s16)(60*1000*X_KHz*Z/4/Line_num/(float)T);//算出的速度单位是r/min
//			/*			      60*Z*（定时器频率f）
//			//最终速度为     --------------------   （r/min）
//							 （4*编码器分辨率）*T
//			*/
//}

/*测试直流电机的机电时间常数的两种数字方法，
注意修改编码器所使用的定时器TIMx->CNT
*/
	/*方法1是使用1KHz的定时中断采样速度，然后画出速度时间曲线，
	0.632倍的最大速度对应的时间即为机电时间常数*/
////			if(Count_num>3000)
////			{
////				Count_num=0;
////				LED0=~LED0;
////				IO_PC4=1;
////				y=1;
////			}
////			
////			if(y==1)
////			{
////				if(i<800)
////				{
////					i++;
////					Speed_data[i]=TIM4->CNT-32760;
////					TIM4->CNT=32760;
////				}
////				else Print_Flag=1;
////			
////			}
	/*方法2
	使用时，中断定时频率是10HZ,测速所用编码器线数至少要300线
	这种计算电机机电时间常数的算法是通过测量电机在响应阶跃输入
	的第一个100MS内脉冲个数和第二100MS内的脉冲个数间接推算的*/
//	      s16 Z1=0;//外部全局变量
//	      s16 Z2=0;	//外部全局变量
//中断函数中内容
//	static u8 x=2,y=0;
//		if(TIM7->SR&0x0001)
//		{
//			if(y==1)
//			{
//				if(x==1)
//				{
//					Z2=TIM4->CNT-32760;
//					TIM4->CNT=32760;
//					x--;
//					Print_Flag=1;
//				}	
//				else if(x==2)
//				{
//					Z1=TIM4->CNT-32760;
//					TIM4->CNT=32760;
//					x--;
//				}
//				else if(x==0)
//					x=0;
//									
//			}
//			Count_num++;
//			if(Count_num>30)
//			{
//				Count_num=0;
//				LED0=~LED0;
//				IO_PC4=1;
//				y=1;
//			}
//			delay_ms(2);

			
	/*			        Z1(第一个100ms)
	//最终速度为 T -  --------------------  (单位是s)，
					  10*Z2（第二个100ms）
	  
	由于电机的机电时间常数一般在10ms左右，故测量的时间选取10倍（远大于）即0.1S
	使用该封装的函数时，中断定时频率必须是1KHZ，才能保证T=0.1S	
			*/
